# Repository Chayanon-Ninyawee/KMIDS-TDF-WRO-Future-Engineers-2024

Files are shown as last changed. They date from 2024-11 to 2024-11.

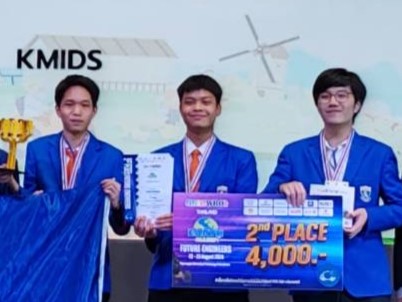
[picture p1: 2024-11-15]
Documentation/Team Picture/Team pic specific.jpg

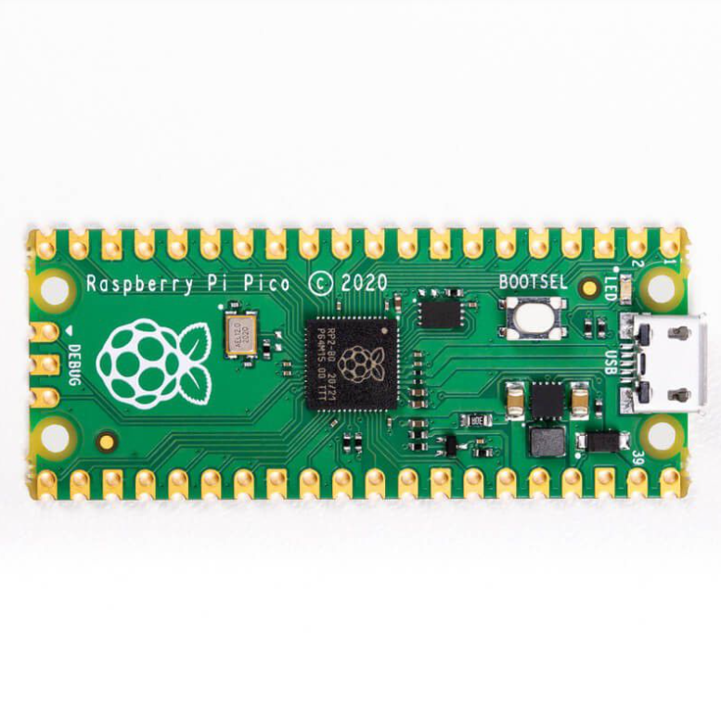
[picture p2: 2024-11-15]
Documentation/Specification/Pi pico.png

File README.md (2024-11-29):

# WRO 2024 Future Engineer
Team: KMIDS Thermodynamically Favorable (KMIDS TDF)

This is a repository for KMIDS Thermodynamically Favorable this project, we aim to design an autonomous robot that can navigate around a field with various rules and restrictions depending on the rounds. In this repository you will find details about our robot: function, design, and reflection from our journey.

New robot
Team member pic

**Member**
- **Left:** Natthapon Itthisathidkulchai (Pao)
- **Middle:** Chayanon Ninyawee (Garfield)
- **Right:** Pannawit Phruithithada (Prame)

## Content
- [RaspberryPi5](https://github.com/Chayanon-Ninyawee/KMIDS-TDF-WRO-Future-Engineers-2024/tree/main/RaspberryPi5) Contains our code for RaspberryPi5 and setup.<!--TODO at link-->
- [RaspberryPiPico](https://github.com/Chayanon-Ninyawee/KMIDS-TDF-WRO-Future-Engineers-2024/tree/main/RaspberryPiPico) Contains our code for RaspberryPiPico and setup.<!--TODO at link-->
- [KMIDS-TDF-WRO2024-FreeCAD](https://github.com/Chayanon-Ninyawee/KMIDS-TDF-WRO-Future-Engineers-2024/tree/main/KMIDS-TDF-WRO2024-FreeCAD) Contains robot's 3D model and electronics.
- [Mobility Management](https://github.com/Chayanon-Ninyawee/KMIDS-TDF-WRO-Future-Engineers-2024/blob/main/Documentation/Mobility_Management/Mobility_Management.md) Contains robot's design and mechanism.
- [Obstacle Management](https://github.com/Chayanon-Ninyawee/KMIDS-TDF-WRO-Future-Engineers-2024/tree/main/Documentation/Obstacle%20Management) Contains how we deal with the obstacle challenges.
- [Power and Senses Management](https://github.com/Chayanon-Ninyawee/KMIDS-TDF-WRO-Future-Engineers-2024/tree/main/Documentation/Power%20and%20Senses%20Management) Contains how we manage our electronics and various sensors.
- [Robot Picture](https://github.com/Chayanon-Ninyawee/KMIDS-TDF-WRO-Future-Engineers-2024/tree/main/Documentation/Robot%20Picture) Contains picture of the robot, both in physical and digital 3D model from FreeCad.
- [Specification](https://github.com/Chayanon-Ninyawee/KMIDS-TDF-WRO-Future-Engineers-2024/tree/main/Documentation/Specification) Contains the specifications of various electronics and parts uses to built this robot.
- [Team Member Picture](https://github.com/Chayanon-Ninyawee/KMIDS-TDF-WRO-Future-Engineers-2024/tree/main/Documentation/Team%20Picture) Contains our team's picture.
- [3D Model](https://github.com/Chayanon-Ninyawee/KMIDS-TDF-WRO-Future-Engineers-2024/tree/fix-readme/Documentation/3D%20model) Contains the process of developing and modeling the chassis.

## Performance video
Our video demonstrating our robot can be found [here](https://youtu.be/9CfIpZZZoUU?si=juIyMaRLtTwPCz_5)
## Design Journey
When designing the robot, our first consideration was its parking strategy. This is a crucial decision, as we had to choose between having the robot reverse into a wall or perform a parallel parking maneuver. Next, we focused on optimizing the robot's turning angle to ensure it could avoid obstacles effectively by maximizing its range of motion. Following that, we moved on to designing the chassis and determining the optimal placement for the various electronic components. A significant challenge during this stage was the limitation of our RPLIDAR C1 sensor, which must be positioned at a precise height to detect the wall properly. Finally, the prototyping phase proved to be the most challenging. We repeatedly faced issues with 3D printing, as the actual printed parts often deviated from the original design, requiring constant adjustments and refinements to achieve the desired results.

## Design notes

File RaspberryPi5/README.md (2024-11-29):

# How to Setup RaspberryPi5
- Insert a microSD card, which should contain 8GB or larger into computer.
- Download, install and run [Raspberry Pi Imager](https://www.raspberrypi.com/software/) that is appropriate for your operating system.
- Click the choose device button and a list of Pi boards appears.
 


- Choose Raspberry Pi 5 in the Pi board. 
  


- Click the Choose OS button and menu will appear. 



- Choose the top choice, Raspberry Pi OS (64-bit), for Pi 5. If there are Raspberry Pi OS on top choice, click that and choose the latest version that works with your board.



- Click Choose Storage and select the card from the menu.



- Click Next 



- Clear and Click Edit Settings 



- Fill in all blank on the General tab: hostname, username / password, wireless LAN (If you plan to use Wi-Fi, and locale settings).



- Go to Serivec Tab, Click Enable SSH button and Select "Use password authentication."  Then click Save.



- Click Yes to apply OS customization settings. !



- Click Yes to confirm that you want to write to your microSD card. !



- It will take a few minutes to download the OS and write it to the card. 



- Once the process is complete, insert the microSD card into your Raspberry Pi, power it on, and give it a few seconds to connect to the network. Then, you can try logging in via SSH, assuming both the Raspberry Pi and your computer are connected to the same Wi-Fi network.

# How to install CMake
``` 
sudo apt install -y cmake
```

# How to Setup OpenCV
## Dependencies
OpenCV needs other software libraries to work, and these must be installed first. Some of them come with the Raspberry Pi 64-bit operating system, and others might already be installed. To be safe, here's the full list. Only the latest packages are installed according to the procedure.
```
# check for updates
sudo apt-get update
sudo apt-get upgrade
# dependencies
sudo apt-get install build-essential cmake git unzip pkg-config
sudo apt-get install libjpeg-dev libpng-dev
sudo apt-get install libavcodec-dev libavformat-dev libswscale-dev
sudo apt-get install libgtk2.0-dev libcanberra-gtk* libgtk-3-dev
sudo apt-get install libgstreamer1.0-dev gstreamer1.0-gtk3
sudo apt-get install libgstreamer-plugins-base1.0-dev gstreamer1.0-gl
sudo apt-get install libxvidcore-dev libx264-dev
sudo apt-get install python3-dev python3-numpy python3-pip
sudo apt-get install libtbb2 libtbb-dev libdc1394-22-dev
sudo apt-get install libv4l-dev v4l-utils
sudo apt-get install libopenblas-dev libatlas-base-dev libblas-dev
sudo apt-get install liblapack-dev gfortran libhdf5-dev
sudo apt-get install libprotobuf-dev libgoogle-glog-dev libgflags-dev
sudo apt-get install protobuf-compiler
```
## Download OpenCV
Once all the third-party software is installed, you can download OpenCV itself. You'll need two packages: the basic version and the additional contributions. After downloading, simply unzip the files. Be careful with line wrapping in the command boxes. The two commands begin with ```wget``` and end with .```zip.```
```
# check your memory first
free -m
# you need at least a total of 5.8 GB!
# if not, enlarge your swap space as explained earlier
# download the latest version
cd ~
git clone --depth=1 https://github.com/opencv/opencv.git
git clone --depth=1 https://github.com/opencv/opencv_contrib.git
```
## Build Make
Before begin with the actual build of the library. You have to make a directory where all the build files can be located.
```
cd ~/opencv
mkdir build
cd build
```
In this step, you instruct CMake on what , where , and how to make OpenCV on your Raspberry Pi. There are several flags to consider, most of which will be familiar to you. One important line you’ll notice is -D WITH_QT=OFF, which disables Qt5 support. If you want to use Qt5 for the GUI, change this to -D WITH_QT=ON. We also save space by excluding any (Python) examples or tests.

Note that there should be spaces before the -D flags, not tabs. Also, the two dots at the end are no typo. It tells CMake where to find its CMakeLists.txt file (the main configuration file); one directory up.
```
cmake -D CMAKE_BUILD_TYPE=RELEASE \
-D CMAKE_INSTALL_PREFIX=/usr/local \
-D OPENCV_EXTRA_MODULES_PATH=~/opencv_contrib/modules \
-D ENABLE_NEON=ON \
-D WITH_OPENMP=ON \
-D WITH_OPENCL=OFF \
-D BUILD_TIFF=ON \
-D WITH_FFMPEG=ON \
-D WITH_TBB=ON \
-D BUILD_TBB=ON \
-D WITH_GSTREAMER=ON \
-D BUILD_TESTS=OFF \
-D WITH_EIGEN=OFF \
-D WITH_V4L=ON \
-D WITH_LIBV4L=ON \
-D WITH_VTK=OFF \
-D WITH_QT=OFF \
-D WITH_PROTOBUF=ON \
-D OPENCV_ENABLE_NONFREE=ON \
-D INSTALL_C_EXAMPLES=OFF \
-D INSTALL_PYTHON_EXAMPLES=OFF \
-D OPENCV_FORCE_LIBATOMIC_COMPILER_CHECK=1 \
-D PYTHON3_PACKAGES_PATH=/usr/lib/python3/dist-packages \
-D OPENCV_GENERATE_PKGCONFIG=ON \
-D BUILD_EXAMPLES=OFF ..
```
CMake comes with a report, showing image below. CMake
## Make
With all compilation directives in place, you can start the build with the following command. This will take about minutes.
```
make -j4
```
Hope that it will show the piture below: 
Install all the generated packages to the database of your system with the next commands.
```
sudo make install
sudo ldconfig
# cleaning (frees 300 KB)
 make clean
sudo apt-get update
```
## Check
Use the following C++ code to check the OpenCV
```
#include <opencv2/opencv.hpp>

int main(void)
{
    std::cout << "OpenCV version : " << cv::CV_VERSION << endl;
    std::cout << "Major version : " << cv::CV_MAJOR_VERSION << endl;
    std::cout << "Minor version : " << cv::CV_MINOR_VERSION << endl;
    std::cout << "Subminor version : " << cv::CV_SUBMINOR_VERSION << endl;
    std::cout << cv::getBuildInformation() << std::endl;
}
```

# How to connect to Raspberry pi 5 via ethernet cable (Open DHCP Server on the Ethernet port in Linux)
- ### Select interface with:
  ```
  sudo nano /etc/default/isc-dhcp-server
  ---
  INTERFACESv4="eno1"
  INTERFACESv6=""

  sudo nano /etc/dhcp/dhcpd.conf
  ---
  subnet 192.168.39.0 netmask 255.255.255.0 {
  range 192.168.39.10 192.168.39.50;
  option subnet-mask 255.255.255.0;
  option routers 192.168.39.1;
  }
  ```

- ### Add new Ethernet Connection
  make the ipv4 address the same as above (192.168.39.1)
- ### How to run:
  ```
  sudo systemctl start isc-dhcp-server.service
  ```
- ### How to check:
  ```
  sudo systemctl status isc-dhcp-server.service
  ```
- ### If error:
  ```
  journalctl _PID=<PID Here>
  ```
- ### Don't forget to make sure the interface is up:
  ```
  ip addr show eno1
  ```
- ### How to autostart:
  ```
  sudo systemctl enable isc-dhcp-server.service
  ```
- ### How to stop autostart:
  ```
  sudo systemctl disable isc-dhcp-server.service
  ```

# ObstacleChallenge Documentation

## Overview

The `ObstacleChallenge` class provides functionality to navigate through obstacle courses using LIDAR and camera data. It incorporates PID controllers for precise control of steering and wall-following distances, state machines for navigation logic, and traffic light detection for enhanced decision-making.

---

## Enums

### `State`
Defines the various states the robot can be in during the obstacle challenge.

- **Values**:
  - `STOP`
  - `NORMAL`
  - `SLOW_BEFORE_TURN`
  - `WAITING_FOR_TURN`
  - `TURNING`
  - `UTURNING_1`
  - `UTURNING_2`
  - `FIND_PARKING_ZONE`
  - `PARKING_1`
  - `PARKING_2`

---

### `TrafficLightRingPosition`
Specifies the ring position of detected traffic lights.

- **Values**:
  - `OUTER`
  - `INNER`

---

### `TrafficLightPosition`
Defines the relative positions of traffic lights.

- **Values**:
  - `BLUE`
  - `MID`
  - `ORANGE`
  - `NO_POSITION`

---

## Structures

### `TrafficLightSearchKey`
Defines a search key for identifying traffic lights.

- **Fields**:
  - `lightPosition`: A `TrafficLightPosition` specifying the traffic light's position.
  - `direction`: A `Direction` enum representing the direction.

#### Operators
- `operator<`: Compares two `TrafficLightSearchKey` objects for ordering.
- `operator==`: Checks equality of two `TrafficLightSearchKey` objects.

#### Hash Function
A custom hash function is defined for use with `std::unordered_set`:
```cpp
namespace std {
    template <>
    struct hash<TrafficLightSearchKey> {
        size_t operator()(const TrafficLightSearchKey& key) const {
            size_t h1 = std::hash<int>{}(static_cast<int>(key.lightPosition));
            size_t h2 = std::hash<int>{}(static_cast<int>(key.direction));
            return h1 ^ (h2 << 1);
        }
    };
}
```

---

## Class: `ObstacleChallenge`

### Constructor
```cpp
ObstacleChallenge(int lidarScale, cv::Point lidarCenter);
```
Initializes an `ObstacleChallenge` object.

- **Parameters**:
  - `lidarScale`: Scale factor for LIDAR data.
  - `lidarCenter`: Center point of the LIDAR map.

---

### Public Methods

#### **`void update`**
```cpp
void update(const cv::Mat& lidarBinaryImage, const cv::Mat& cameraImage, float gyroYaw, float& motorPercent, float& steeringPercent);
```
Updates the robot's state and controls motor and steering based on sensor inputs.

- **Parameters**:
  - `lidarBinaryImage`: Binary image from the LIDAR data.
  - `cameraImage`: Image captured from the camera.
  - `gyroYaw`: Current yaw angle from the gyroscope.
  - `motorPercent`: Motor speed percentage (output parameter).
  - `steeringPercent`: Steering angle percentage (output parameter).

---

### Private Members

#### **PID Controllers**
- `steeringPID`: Controls steering with parameters `Kp = 0.026f`, `Ki = 0.0f`, `Kd = 0.0008f`.
- `wallDistancePID`: Controls wall-following distance with parameters `Kp = 200.0f`, `Ki = 0.0010f`, `Kd = 0.0f`.

#### **Thresholds and Biases**
- `MAX_HEADING_ERROR`: Maximum allowable heading error (`40.0` degrees).
- `MIN_HEADING_ERROR`: Minimum allowable heading error (`-40.0` degrees).
- `FRONT_WALL_DISTANCE_*`: Various thresholds for wall distances, used to make decisions during navigation.
- `wallDistanceBias`: Bias for wall distance control (`0.0f` by default).

#### **State and Cooldown Timers**
- `state`: Current state of the robot (`State::NORMAL` by default).
- `TURN_COOLDOWN`: Cooldown time between turns (`1.1f` seconds).
- `FIND_PARKING_COOLDOWN`: Cooldown time for parking detection (`1.1f` seconds).
- `TRAFFIC_COOLDOWN`: Cooldown time for traffic light processing (`0.8f` seconds).

#### **Traffic Light Handling**
- `trafficLightMap`: Maps `TrafficLightSearchKey` to ring position and color.
- `trafficLightOrderQueue`: Maintains the insertion order of traffic light keys.
- `trafficLightKeySet`: Ensures fast duplicate detection of traffic lights.

#### **Miscellaneous**
- `robotDirection`: Current direction of the robot (`NORTH` by default).
- `turnDirection`: Current turn direction (`UNKNOWN` by default).
- `numberofTurn`: Number of turns completed.

---

## Example Usage
```cpp
#include "ObstacleChallenge.h"
#include <opencv2/opencv.hpp>

int main() {
    cv::Point lidarCenter(100, 100);
    int lidarScale = 10;

    ObstacleChallenge obstacleChallenge(lidarScale, lidarCenter);

    cv::Mat lidarBinaryImage; // Load or initialize LIDAR image
    cv::Mat cameraImage;      // Load or initialize camera image
    float gyroYaw = 0.0f;
    float motorPercent = 0.0f;
    float steeringPercent = 0.0f;

    obstacleChallenge.update(lidarBinaryImage, cameraImage, gyroYaw, motorPercent, steeringPercent);

    // Use motorPercent and steeringPercent as needed
    return 0;
}
```

---

## Licensing

This header file should be used in compliance with the licensing terms of its respective project and dependencies, including OpenCV and any LIDAR processing libraries.

# OpenChallenge Documentation

## Overview

The `OpenChallenge` class provides the logic for navigating an open space using LIDAR data. It employs PID controllers to manage steering and wall distance, and a state machine to handle transitions between different navigation states.

---

## Enums

### `State`
Defines the possible states of the robot during the open challenge.

- **Values**:
  - `STOP`: The robot is stopped.
  - `NORMAL`: The robot is moving forward under normal conditions.
  - `TURNING`: The robot is in a turning state.

---

## Class: `OpenChallenge`

### Constructor
```cpp
OpenChallenge(int lidarScale, cv::Point lidarCenter);
```
Initializes an `OpenChallenge` object.

- **Parameters**:
  - `lidarScale`: Scale factor for the LIDAR data.
  - `lidarCenter`: The center point of the LIDAR map.

---

### Public Methods

#### **`void update`**
```cpp
void update(const cv::Mat& lidarBinaryImage, float gyroYaw, float& motorPercent, float& steeringPercent);
```
Updates the robot's motor and steering outputs based on the LIDAR image and gyro data.

- **Parameters**:
  - `lidarBinaryImage`: Binary image representing the LIDAR data.
  - `gyroYaw`: Current yaw angle from the gyroscope.
  - `motorPercent`: Output parameter for motor speed as a percentage (-1.0 to 1.0).
  - `steeringPercent`: Output parameter for steering angle as a percentage (-1.0 to 1.0).

---

### Private Members

#### **PID Controllers**
- `steeringPID`: Controls steering with parameters:
  - `Kp = 0.017f`
  - `Ki = 0.0f`
  - `Kd = 0.0019f`
- `wallDistancePID`: Controls wall-following with parameters:
  - `Kp = 50.0f`
  - `Ki = 0.0f`
  - `Kd = 0.0030f`

#### **Thresholds and Biases**
- `MAX_HEADING_ERROR`: Maximum allowable heading error (`25.0` degrees).
- `MIN_HEADING_ERROR`: Minimum allowable heading error (`-25.0` degrees).
- `FRONT_WALL_DISTANCE_STOP_THRESHOLD`: Distance at which the robot stops moving forward (`2.200` meters).
- `FRONT_WALL_DISTANCE_SLOWDOWN_THRESHOLD`: Distance at which the robot slows down (`1.000` meters).
- `FRONT_WALL_DISTANCE_TURN_THRESHOLD`: Distance at which the robot initiates a turn (`0.690` meters).
- `OUTER_WALL_DISTANCE`: Distance to maintain from the outer wall (`0.350` meters).
- `MAX_HEADING_ERROR_BEFORE_EXIT_TURNING`: Maximum heading error allowed before exiting a turning state (`10.0` degrees).
- `wallDistanceBias`: Wall distance bias (`0.000` by default, where negative is left bias and positive is right bias).

#### **State and Cooldown Timers**
- `state`: Current state of the robot (`State::NORMAL` by default).
- `lastTurnTime`: Time of the last turn made (`-1.0` seconds by default).
- `TURN_COOLDOWN`: Cooldown time between consecutive turns (`1.0` seconds).
- `STOP_COOLDOWN`: Cooldown time before stopping after a turn (`0.2` seconds).

#### **Navigation Parameters**
- `lidarScale`: Scale of the LIDAR data.
- `lidarCenter`: Center point of the LIDAR map.
- `robotDirection`: Current direction of the robot (`NORTH` by default).
- `turnDirection`: Current turn direction (`UNKNOWN` by default).
- `numberofTurn`: Number of turns completed.

---

## Example Usage

```cpp
#include "OpenChallenge.h"
#include <opencv2/opencv.hpp>

int main() {
    cv::Point lidarCenter(100, 100);
    int lidarScale = 10;

    OpenChallenge openChallenge(lidarScale, lidarCenter);

    cv::Mat lidarBinaryImage; // Initialize or load LIDAR binary image
    float gyroYaw = 0.0f;
    float motorPercent = 0.0f;
    float steeringPercent = 0.0f;

    openChallenge.update(lidarBinaryImage, gyroYaw, motorPercent, steeringPercent);

    // Use motorPercent and steeringPercent for robot control
    return 0;
}
```

---

## Licensing

This file should be used in compliance with the licensing terms of its respective project and any dependencies such as OpenCV.

# BNO055 Struct Documentation

## Overview

This header file defines structures for handling BNO055 sensor data outputs in precision floating-point format. The structures encapsulate data for accelerometer readings and Euler angles.

---

## Structs

### `bno055_accel_float_t`
A structure representing accelerometer output data in floating-point precision.

#### Fields
- `x`: Accelerometer data along the X-axis.
- `y`: Accelerometer data along the Y-axis.
- `z`: Accelerometer data along the Z-axis.

#### Example
```cpp
bno055_accel_float_t accelData;
accelData.x = 1.23f;
accelData.y = 0.45f;
accelData.z = -0.67f;
```

---

### `bno055_euler_float_t`
A structure representing Euler angle output data in floating-point precision.

#### Fields
- `h`: Heading (yaw) angle in degrees.
- `r`: Roll angle in degrees.
- `p`: Pitch angle in degrees.

#### Example
```cpp
bno055_euler_float_t eulerData;
eulerData.h = 90.0f;
eulerData.r = -45.0f;
eulerData.p = 10.0f;
```

---

## Licensing

This file should be used in compliance with the licensing terms of the project it belongs to. The structures are designed for BNO055 sensor integration and should adhere to the sensor's usage guidelines.

---
**Header Guard**: 
```cpp
#ifndef BNO055_STRUCT_H
#define BNO055_STRUCT_H
```
Ensure this file is included only once during compilation.

# DataSaver Documentation

## Overview

The `DataSaver` namespace provides functionality for saving and loading various types of data, including calibration data, LIDAR scan data, BNO055 sensor data, and images. These utilities are designed to simplify data logging and retrieval for robotics applications.

---

## Functions

### `bool saveData`
```cpp
bool saveData(const std::string& filePath, const uint8_t calibData[22], bool append = true);
```
Saves calibration data to a file.

- **Parameters**:
  - `filePath`: Path to the file where the data will be saved.
  - `calibData`: Array containing 22 bytes of calibration data.
  - `append`: If `true`, appends the data to the file (default is `true`).

- **Returns**:
  - `true` if the data was saved successfully, `false` otherwise.

---

### `bool loadData`
```cpp
bool loadData(const std::string& filePath, uint8_t calibData[22]);
```
Loads calibration data from a file.

- **Parameters**:
  - `filePath`: Path to the file from which the data will be loaded.
  - `calibData`: Array to store the 22 bytes of loaded calibration data.

- **Returns**:
  - `true` if the data was loaded successfully, `false` otherwise.

---

### `bool saveLogData`
```cpp
bool saveLogData(const std::string& filePath, 
                 const std::vector<lidarController::NodeData>& scanData, 
                 const bno055_accel_float_t& accel_data, 
                 const bno055_euler_float_t& euler_data, 
                 const cv::Mat& image, 
                 bool append = true);
```
Saves log data including LIDAR scans, accelerometer data, Euler data, and an image.

- **Parameters**:
  - `filePath`: Path to the file where the log data will be saved.
  - `scanData`: Vector of LIDAR scan data.
  - `accel_data`: Accelerometer data (`bno055_accel_float_t`).
  - `euler_data`: Euler angle data (`bno055_euler_float_t`).
  - `image`: Image (`cv::Mat`) to be saved.
  - `append`: If `true`, appends the log data to the file (default is `true`).

- **Returns**:
  - `true` if the log data was saved successfully, `false` otherwise.

---

### `bool loadLogData`
```cpp
bool loadLogData(const std::string& filePath, 
                 std::vector<std::vector<lidarController::NodeData>>& allScanData, 
                 std::vector<bno055_accel_float_t>& allAccelData, 
                 std::vector<bno055_euler_float_t>& allEulerData, 
                 std::vector<cv::Mat>& allImages);
```
Loads log data including LIDAR scans, accelerometer data, Euler data, and images.

- **Parameters**:
  - `filePath`: Path to the file from which the log data will be loaded.
  - `allScanData`: Vector to store multiple sets of LIDAR scan data.
  - `allAccelData`: Vector to store accelerometer data.
  - `allEulerData`: Vector to store Euler angle data.
  - `allImages`: Vector to store images (`cv::Mat`).

- **Returns**:
  - `true` if the log data was loaded successfully, `false` otherwise.

---

## Namespace: `DataSaver`

The functions are encapsulated within the `DataSaver` namespace to avoid name conflicts and improve organization.

---

## Licensing

This file is part of a robotics project and should be used in accordance with its licensing terms.

---
**Header Guard**:
```cpp
#ifndef DATASAVER_H
#define DATASAVER_H
```N    
Ensure this file is included only once during compilation.
# Direction Header Documentation

## Overview

This header file defines enums and functions for managing cardinal and relative directions, including utilities for turning and converting directions to string or heading values.

---

## Enums

### `Direction`
Represents the four cardinal directions.

#### Values:
- `NORTH`
- `EAST`
- `SOUTH`
- `WEST`

---

### `RelativeDirection`
Represents relative movement directions.

#### Values:
- `FRONT`
- `BACK`
- `LEFT`
- `RIGHT`

---

### `TurnDirection`
Represents the possible turn directions.

#### Values:
- `CLOCKWISE`
- `COUNTER_CLOCKWISE`
- `UNKNOWN`

---

## Functions

### `Direction calculateRelativeDirection`
```cpp
Direction calculateRelativeDirection(Direction currentDirection, RelativeDirection relativeMove);
```

Calculates the new direction based on the current direction and a relative move.

#### Parameters:
- `currentDirection`: The current cardinal direction (`Direction`).
- `relativeMove`: The relative move to apply (`RelativeDirection`).

#### Returns:
- A `Direction` representing the new cardinal direction.

#### Example:
```cpp
Direction newDir = calculateRelativeDirection(NORTH, RIGHT);
// newDir will be EAST
```

---

### `std::string directionToString`
```cpp
std::string directionToString(Direction direction);
```

Converts a `Direction` enum value to a human-readable string.

#### Parameters:
- `direction`: A `Direction` enum value.

#### Returns:
- A string representation of the direction (e.g., "NORTH", "EAST").

#### Example:
```cpp
std::string dirStr = directionToString(WEST);
// dirStr will be "WEST"
```

---

### `float directionToHeading`
```cpp
float directionToHeading(Direction direction);
```

Converts a `Direction` enum value to a heading angle in degrees.

#### Parameters:
- `direction`: A `Direction` enum value.

#### Returns:
- A float representing the heading in degrees:
  - `NORTH` → 0°
  - `EAST` → 90°
  - `SOUTH` → 180°
  - `WEST` → 270°

#### Example:
```cpp
float heading = directionToHeading(SOUTH);
// heading will be 180.0f
```

---

## Licensing

This file is part of a robotics or navigation project. Use in compliance with the project's licensing terms.

---

**Header Guard**:
```cpp
#ifndef DIRECTION_H
#define DIRECTION_H
```

Prevents multiple inclusions during compilation.

# I2C Master Library Documentation

This documentation provides an overview of the `i2c_master` library, designed to manage I2C communication between a master device and a slave device. The library includes memory mapping, command structures, and utility functions for sending and receiving data.

## Namespace: `i2c_slave_mem_addr`
Defines memory layout and sizes for the I2C slave's memory map.

### Constants:
- **`MEM_SIZE`**: Total memory size (256 bytes).
- **`COMMAND_SIZE`**: Command register size (1 byte).
- **`STATUS_SIZE`**: Status register size (1 byte).
- **`GYRO_OFFSET_SIZE`**: Gyroscope offset data size (6 bytes).
- **`ACCEL_OFFSET_SIZE`**: Accelerometer offset data size (8 bytes).
- **`MAG_OFFSET_SIZE`**: Magnetometer offset data size (8 bytes).
- **`BNO055_CALIB_SIZE`**: Total calibration data size (22 bytes).
- **`ACCEL_DATA_SIZE`**: Accelerometer data size (12 bytes).
- **`EULER_ANGLE_SIZE`**: Euler angle data size (12 bytes).
- **`BNO055_INFO_SIZE`**: Total sensor info size (24 bytes).
- **`MOTOR_PERCENT_SIZE`**: Motor speed as float (4 bytes).
- **`STEERING_PERCENT_SIZE`**: Steering angle as float (4 bytes).
- **`MOVEMENT_INFO_SIZE`**: Combined movement info size (8 bytes).
- **`LOG_SIZE`**: Size of each log entry (1 byte).
- **`LOGS_BUFFER_SIZE`**: Total logs buffer size (256 bytes).

### Memory Map Addresses:
- **`COMMAND_ADDR`**: Start address of command data.
- **`STATUS_ADDR`**: Start address of status data.
- **`BNO055_CALIB_ADDR`**: Start address of calibration data.
- **`BNO055_INFO_ADDR`**: Start address of sensor info.
- **`MOVEMENT_INFO_ADDR`**: Start address of movement info.
- **`LOG_ADDR`**: Start address of log data.

### Static Assertions:
Ensures memory allocation fits within the defined buffer size.

---

## Enums

### `Command`
Defines available commands for the I2C slave device:
- **`NO_COMMAND (0x00)`**: No operation.
- **`RESTART (0x01)`**: Restart the slave device.
- **`CALIB_NO_OFFSET (0x02)`**: Calibrate without offsets.
- **`CALIB_WITH_OFFSET (0x03)`**: Calibrate with offsets.
- **`SKIP_CALIB (0x04)`**: Skip calibration.

---

## Functions

### Initialization and Setup
#### `int i2c_master_init(uint8_t slave_address)`
Initializes communication with the I2C slave device.
- **Parameters**:
  - `slave_address`: 7-bit address of the I2C slave device.
- **Returns**: File descriptor for the I2C device, or `-1` on failure.

---

### Command and Data Transmission
#### `void i2c_master_send_command(int fd, uint8_t command)`
Sends a command to the I2C slave device.
- **Parameters**:
  - `fd`: File descriptor for the I2C device.
  - `command`: Command byte.

#### `void i2c_master_send_data(int fd, uint8_t reg, uint8_t *data, uint8_t len)`
Sends data to a specific register on the I2C slave device.
- **Parameters**:
  - `fd`: File descriptor for the I2C device.
  - `reg`: Register address to write to.
  - `data`: Pointer to the data buffer.
  - `len`: Length of the data buffer.

#### `void i2c_master_read_data(int fd, uint8_t reg, uint8_t *data, uint8_t len)`
Reads data from a specific register on the I2C slave device.
- **Parameters**:
  - `fd`: File descriptor for the I2C device.
  - `reg`: Register address to read from.
  - `data`: Pointer to the buffer for storing the data.
  - `len`: Number of bytes to read.

---

### Logging Functions
#### `void i2c_master_read_logs(int fd, uint8_t *logs)`
Reads log data from the I2C slave using the default size.
- **Parameters**:
  - `fd`: File descriptor for the I2C device.
  - `logs`: Pointer to the buffer for storing logs.

#### `void i2c_master_read_logs(int fd, uint8_t *logs, size_t len)`
Reads log data with a specified size.
- **Parameters**:
  - `fd`: File descriptor for the I2C device.
  - `logs`: Pointer to the buffer for storing logs.
  - `len`: Number of bytes to read.

#### `void i2c_master_print_logs(uint8_t *logs, size_t len)`
Prints logs in a human-readable format.
- **Parameters**:
  - `logs`: Pointer to the log data buffer.
  - `len`: Length of the log buffer.

---

### Reading Specific Data
#### `void i2c_master_read_command(int fd, uint8_t *command)`
Reads the command byte from the slave.
- **Parameters**:
  - `fd`: File descriptor for the I2C device.
  - `command`: Pointer to the buffer for storing the command byte.

#### `void i2c_master_read_status(int fd, uint8_t *status)`
Reads the status byte from the slave.
- **Parameters**:
  - `fd`: File descriptor for the I2C device.
  - `status`: Pointer to the buffer for storing the status byte.

#### `void i2c_master_read_bno055_calibration(int fd, uint8_t *calibration_data)`
Reads calibration data from the BNO055 sensor.
- **Parameters**:
  - `fd`: File descriptor for the I2C device.
  - `calibration_data`: Pointer to the buffer for storing calibration data.

#### `void i2c_master_read_bno055_info(int fd, uint8_t *info_data)`
Reads sensor data (acceleration and Euler angles).
- **Parameters**:
  - `fd`: File descriptor for the I2C device.
  - `info_data`: Pointer to the buffer for storing sensor data.

#### `void i2c_master_read_movement_info(int fd, uint8_t *movement_info)`
Reads movement information (motor and steering percentages).
- **Parameters**:
  - `fd`: File descriptor for the I2C device.
  - `movement_info`: Pointer to the buffer for storing movement info.

#### `void i2c_master_read_bno055_accel_and_euler(int fd, bno055_accel_float_t *accel_data, bno055_euler_float_t *euler_data)`
Reads both acceleration and Euler angle data from the BNO055.
- **Parameters**:
  - `fd`: File descriptor for the I2C device.
  - `accel_data`: Pointer to the structure for storing acceleration data.
  - `euler_data`: Pointer to the structure for storing Euler angle data.

---

## Conclusion

The `i2c_master` library provides comprehensive support for I2C communication with a focus on sensor data retrieval, logging, and calibration. The modular design ensures easy integration into larger systems.
# Image Processor Library Documentation

This document provides an overview of the `image_processor` library, which uses OpenCV for image processing tasks such as detecting lines, identifying blocks, and processing specific color ranges.

---

## Constants

### General
- **`CROP_PERCENT`**: Ratio to crop the image for processing (50%).

### Color Ranges
Defined as `cv::Scalar` values for lower and upper HSV bounds to detect specific colors:
- **Blue Line**: 
  - `lowerBlueLine = (100, 100, 150)`
  - `upperBlueLine = (140, 220, 220)`
- **Orange Line**: 
  - `lowerOrangeLine = (6, 120, 180)`
  - `upperOrangeLine = (16, 230, 255)`
- **Red Line**: 
  - `lowerRed1Light = (0, 135, 160)`
  - `upperRed1Light = (2, 205, 255)`
  - `lowerRed2Light = (175, 135, 160)`
  - `upperRed2Light = (180, 205, 255)`
- **Green Line**: 
  - `lowerGreen1Light = (55, 70, 120)`
  - `upperGreen1Light = (84, 175, 195)`
  - `lowerGreen2Light = (84, 175, 195)`
  - `upperGreen2Light = (84, 175, 195)`
- **Pink**: 
  - `lowerPinkLight = (165, 244, 200)`
  - `upperPinkLight = (171, 255, 255)`

### Minimum Contour Areas
- **`minBlueLineArea = 37`**
- **`minOrangeLineArea = 37`**
- **`minRedLineArea = 300`**
- **`minGreenLineArea = 300`**

---

## Enums

### `enum class Color`
Defines the color categories used for block detection:
- **`BLUE`**
- **`ORANGE`**
- **`RED`**
- **`GREEN`**
- **`PINK`**

---

## Structs

### `struct Block`
Represents a detected block in the image.
- **`int x`**: X-coordinate of the block.
- **`int y`**: Y-coordinate of the block.
- **`int lowestY`**: Lowest Y-coordinate (for vertical alignment).
- **`int size`**: Size of the block.
- **`Color color`**: Detected color of the block.

### `struct ImageProcessingResult`
Stores the results of the image processing operations.
- **`int blueLineY`**: Y-coordinate of the blue line.
- **`int blueLineSize`**: Size of the blue line.
- **`int orangeLineY`**: Y-coordinate of the orange line.
- **`int orangeLineSize`**: Size of the orange line.
- **`std::vector<Block> blocks`**: Detected blocks.
- **`int pinkX`**: X-coordinate of the pink region.
- **`int pinkY`**: Y-coordinate of the pink region.
- **`int pinkSize`**: Size of the pink region.

---

## Functions

### Utility Functions
#### `std::vector<cv::Point> getCoordinates(const cv::Mat &mask)`
Extracts the coordinates of non-zero pixels in a mask.
- **Parameters**:
  - `mask`: Binary image mask.
- **Returns**: Vector of points with non-zero values.

#### `int getAverageX(const std::vector<cv::Point> &coordinates)`
Calculates the average X-coordinate.
- **Parameters**:
  - `coordinates`: Vector of points.
- **Returns**: Average X-coordinate.

#### `int getAverageY(const std::vector<cv::Point> &coordinates)`
Calculates the average Y-coordinate.
- **Parameters**:
  - `coordinates`: Vector of points.
- **Returns**: Average Y-coordinate.

#### `std::tuple<cv::Point, double, cv::Point> getCentroidAndArea(const std::vector<cv::Point> &contour)`
Calculates the centroid and area of a given contour.
- **Parameters**:
  - `contour`: Vector of points representing a contour.
- **Returns**: Tuple containing:
  - Centroid point.
  - Area of the contour.
  - Additional point for extended centroid information.

---

### Image Processing
#### `ImageProcessingResult processImage(const cv::Mat &image)`
Processes the input image to detect lines, blocks, and colored regions.
- **Parameters**:
  - `image`: Input image.
- **Returns**: Processed results in an `ImageProcessingResult` structure.

#### `cv::Mat filterAllColors(const cv::Mat &image)`
Applies color filtering to detect and highlight all defined color ranges.
- **Parameters**:
  - `image`: Input image.
- **Returns**: Processed image with color filters applied.

---

### Visualization
#### `cv::Mat drawImageProcessingResult(const ImageProcessingResult &result, cv::Mat &image)`
Draws the processing results (lines, blocks, and pink regions) on the input image.
- **Parameters**:
  - `result`: Processing results to visualize.
  - `image`: Input image to draw on.
- **Returns**: Image with visualizations.

---

### Conversion
#### `float pixelToAngle(int pixelX, int imageWidth, int centerOffset, float fov)`
Converts a pixel position to an angle relative to the image's field of view (FoV).
- **Parameters**:
  - `pixelX`: X-coordinate of the pixel.
  - `imageWidth`: Width of the image.
  - `centerOffset`: Offset for the center point.
  - `fov`: Field of view of the camera.
- **Returns**: Angle in degrees.

---

## Conclusion
The `image_processor` library provides comprehensive tools for color-based image analysis and line/block detection. Its modular structure supports real-time processing and visualization for robotics and computer vision applications.
# LibCamera Library Documentation

This documentation details the functionality of the `LibCamera` class, which provides a C++ interface to manage and interact with cameras using the `libcamera` library.

---

## Includes and Dependencies
The library depends on the following headers and libraries:
- **Standard Libraries**:
  - `<atomic>`: For atomic operations.
  - `<iomanip>`: For formatted output.
  - `<iostream>`: For input/output operations.
  - `<limits.h>`: For defining data type limits.
  - `<memory>`: For smart pointers.
  - `<stdint.h>`: For fixed-width integer types.
  - `<string>`: For string manipulation.
  - `<vector>`: For dynamic arrays.
  - `<unordered_map>`: For hash tables.
  - `<queue>`: For FIFO data structure.
  - `<sstream>`: For string streams.
  - `<sys/mman.h>`: For memory management.
  - `<unistd.h>`: For POSIX APIs.
  - `<time.h>`: For time operations.
  - `<mutex>`: For thread synchronization.

- **Libcamera Libraries**:
  - `<libcamera/controls.h>`: For camera control operations.
  - `<libcamera/control_ids.h>`: For control ID management.
  - `<libcamera/property_ids.h>`: For accessing camera properties.
  - `<libcamera/libcamera.h>`: Core libcamera library.
  - `<libcamera/camera.h>`: For camera management.
  - `<libcamera/camera_manager.h>`: For managing camera instances.
  - `<libcamera/framebuffer_allocator.h>`: For allocating frame buffers.
  - `<libcamera/request.h>`: For request handling.
  - `<libcamera/stream.h>`: For stream management.
  - `<libcamera/formats.h>`: For handling data formats.
  - `<libcamera/transform.h>`: For image transformations.

---

## Structs

### `LibcameraOutData`
Represents output data from the camera.
- **`uint8_t *imageData`**: Pointer to the image data.
- **`uint32_t size`**: Size of the image data in bytes.
- **`uint64_t request`**: Identifier for the request.

---

## Class: `LibCamera`

### Overview
The `LibCamera` class is responsible for initializing, configuring, and interacting with a camera device. It supports operations such as capturing frames, setting controls, and managing camera streams.

---

### Public Methods

#### Constructor and Destructor
- **`LibCamera()`**: Default constructor.
- **`~LibCamera()`**: Destructor to clean up resources.

#### Camera Initialization and Configuration
- **`int initCamera()`**: Initializes the camera.
- **`void configureStill(int width, int height, PixelFormat format, int buffercount, Orientation orientation)`**:
  Configures the camera for still image capture.
  - **Parameters**:
    - `width`: Desired image width.
    - `height`: Desired image height.
    - `format`: Pixel format for the images.
    - `buffercount`: Number of frame buffers.
    - `orientation`: Camera orientation.

#### Camera Control and State
- **`int startCamera()`**: Starts the camera capture session.
- **`int resetCamera(int width, int height, PixelFormat format, int buffercount, Orientation orientation)`**:
  Resets the camera with new configuration parameters.
- **`void stopCamera()`**: Stops the camera capture session.
- **`void closeCamera()`**: Closes and releases the camera.

#### Frame Handling
- **`bool readFrame(LibcameraOutData *frameData)`**:
  Reads a frame from the camera.
  - **Parameters**:
    - `frameData`: Pointer to the output frame data structure.
  - **Returns**: `true` if successful, `false` otherwise.
- **`void returnFrameBuffer(LibcameraOutData frameData)`**:
  Returns the frame buffer to the camera for reuse.

#### Control Management
- **`void set(ControlList controls)`**: Sets camera controls using a `ControlList`.

#### Stream Management
- **`Stream *VideoStream(uint32_t *w, uint32_t *h, uint32_t *stride) const`**:
  Retrieves the video stream dimensions.
  - **Parameters**:
    - `w`: Pointer to store the width.
    - `h`: Pointer to store the height.
    - `stride`: Pointer to store the stride.
  - **Returns**: Pointer to the video stream.

#### Camera Information
- **`char *getCameraId()`**: Retrieves the unique identifier of the camera.

---

### Private Methods

#### Capture and Request Management
- **`int startCapture()`**: Begins capturing frames.
- **`int queueRequest(Request *request)`**:
  Queues a request for processing.
  - **Parameters**:
    - `request`: Pointer to the request.
- **`void requestComplete(Request *request)`**:
  Handles a completed request.
- **`void processRequest(Request *request)`**:
  Processes the request and extracts data.

#### Stream Utility
- **`void StreamDimensions(Stream const *stream, uint32_t *w, uint32_t *h, uint32_t *stride) const`**:
  Gets the dimensions of a specific stream.
  - **Parameters**:
    - `stream`: Pointer to the stream.
    - `w`: Pointer to store the width.
    - `h`: Pointer to store the height.
    - `stride`: Pointer to store the stride.

---

### Private Members
- **Camera and Manager**:
  - `unsigned int cameraIndex_`: Index of the camera.
  - `uint64_t last_`: Timestamp of the last operation.
  - `std::unique_ptr<CameraManager> cm`: Camera manager instance.
  - `std::shared_ptr<Camera> camera_`: Shared pointer to the camera.
  - `std::unique_ptr<CameraConfiguration> config_`: Configuration for the camera.
  - `std::unique_ptr<FrameBufferAllocator> allocator_`: Allocator for frame buffers.

- **Request Management**:
  - `std::vector<std::unique_ptr<Request>> requests_`: List of requests.
  - `std::queue<Request *> requestQueue`: Queue of requests.

- **Buffer Management**:
  - `std::map<int, std::pair<void *, unsigned int>> mappedBuffers_`: Mapped buffers for frame data.

- **Streams**:
  - `Stream *viewfinder_stream_`: Pointer to the viewfinder stream.

- **Controls and Synchronization**:
  - `ControlList controls_`: Current controls.
  - `std::mutex control_mutex_`: Mutex for control operations.
  - `std::mutex camera_stop_mutex_`: Mutex for stopping the camera.
  - `std::mutex free_requests_mutex_`: Mutex for managing free requests.

- **Camera Metadata**:
  - `std::string cameraId`: Identifier of the camera.

---

## Conclusion
The `LibCamera` class encapsulates the complexities of working with `libcamera`, offering a high-level interface for camera operations. It supports advanced features such as request management, stream handling, and control configuration, making it suitable for applications requiring precise camera control and data capture.

# LidarController.h Documentation

## Overview

The `LidarController` class provides functionality for controlling and acquiring data from a SLAMTEC LIDAR device. It handles initialization, scanning, data retrieval, and shutdown procedures for the LIDAR sensor.

## Class: `LidarController`

### Constructor: `LidarController(const char* serialPort = "/dev/ttyAMA0", int baudRate = 460800)`
- **Description**: Initializes the `LidarController` object with the provided serial port and baud rate.
- **Parameters**:
  - `serialPort` (default `"/dev/ttyAMA0"`) - The serial port path used to communicate with the LIDAR device.
  - `baudRate` (default `460800`) - Baud rate for communication with the LIDAR device.

### Destructor: `~LidarController()`
- **Description**: Cleans up resources and shuts down the LIDAR when the object is destroyed.

### Method: `bool initialize()`
- **Description**: Initializes the LIDAR driver and establishes a connection with the device.
- **Returns**: `true` if the initialization is successful, `false` otherwise.

### Method: `bool startScanning()`
- **Description**: Starts scanning using the LIDAR. This initiates the motor spin and begins data acquisition.
- **Returns**: `true` if the scan starts successfully, `false` otherwise.

### Method: `void stopScanning()`
- **Description**: Stops the LIDAR scanning process and halts the motor.

### Method: `std::vector<NodeData> getScanData()`
- **Description**: Retrieves scan data from the LIDAR, including angles and distances.
- **Returns**: A vector of `NodeData` containing the scan results.

### Method: `void shutdown()`
- **Description**: Shuts down the LIDAR, stops scanning, and cleans up all resources.

### Method: `static void printScanData(const std::vector<NodeData>& nodeDataVector)`
- **Description**: Prints the LIDAR scan data to the console.
- **Parameters**:
  - `nodeDataVector` - A vector of `NodeData` containing the scan results to be printed.

## Private Members

- `sl::ILidarDriver* lidarDriver` - A pointer to the LIDAR driver instance.
- `sl::IChannel* serialChannel` - A pointer to the communication channel.
- `const char* serialPort` - The serial port used for LIDAR connection.
- `int baudRate` - Baud rate for the communication.

## Dependencies

- `sl_lidar.h` and `sl_lidar_driver.h` - Headers for interacting with the SLAMTEC LIDAR.
- `lidar_struct.h` - A header containing the `NodeData` structure and other necessary definitions.

## Notes
- The `LidarController` class requires a valid SLAMTEC LIDAR device and an appropriate serial port for communication.
# LIDAR Data Processor Documentation

## Overview
The `LIDAR Data Processor` is a C++ library that processes LIDAR data for detecting and analyzing traffic lights, parking zones, and walls. It works by converting raw LIDAR data into a 2D image for further processing using OpenCV techniques. The library can also detect lines, calculate angles, and process data to determine directions for navigation.

## Structures

### `BlockInfo`
Contains information about each detected block in the LIDAR scan.

- `float angle`: The angle of the detected block in degrees.
- `int size`: The size of the block.
- `Color color`: The color of the traffic light associated with the block.

### `ProcessedTrafficLight`
Contains information about each detected traffic light.

- `cv::Point point`: The location of the block.
- `int size`: The size of the block.
- `Color color`: The color of the traffic light.

## Functions

### `cv::Mat lidarDataToImage(const std::vector<lidarController::NodeData> &data, int width, int height, float scale)`
Converts raw LIDAR data into a grayscale OpenCV image. The image will be scaled based on the provided scale factor.

- **Parameters**:
  - `data`: A vector containing the LIDAR data points.
  - `width`: The width of the output image.
  - `height`: The height of the output image.
  - `scale`: A scaling factor to adjust the image resolution.
  
- **Returns**: A grayscale OpenCV image.

### `float toMeter(int scale, double lidarDistance)`
Converts a LIDAR distance into meters, based on the scaling factor.

- **Parameters**:
  - `scale`: The scale factor used for the conversion.
  - `lidarDistance`: The raw distance from the LIDAR.
  
- **Returns**: The distance in meters.

### `std::vector<cv::Vec4i> detectLines(const cv::Mat &binaryImage)`
Detects lines in a binary image using the Hough Line Transform.

- **Parameters**:
  - `binaryImage`: The binary image (after thresholding) to detect lines in.

- **Returns**: A vector of lines represented by four values: `(x1, y1, x2, y2)` for each detected line.

### `double lineLength(const cv::Vec4i& line)`
Calculates the length of a line from the vector `(x1, y1, x2, y2)`.

- **Parameters**:
  - `line`: A vector representing the line with its endpoints.

- **Returns**: The length of the line.

### `double calculateAngle(const cv::Vec4i &line)`
Calculates the angle of a line in degrees.

- **Parameters**:
  - `line`: A vector representing the line with its endpoints.

- **Returns**: The angle of the line in degrees.

### `double pointLinePerpendicularDistance(const cv::Point2f& pt, const cv::Vec4i& line)`
Calculates the perpendicular distance from a point to a line.

- **Parameters**:
  - `pt`: A point.
  - `line`: A line represented by a vector of four points.

- **Returns**: The perpendicular distance from the point to the line.

### `double pointLinePerpendicularDirection(const cv::Point2f& pt, const cv::Vec4i& line)`
Calculates the perpendicular direction from a point to a line.

- **Parameters**:
  - `pt`: A point.
  - `line`: A line represented by a vector of four points.

- **Returns**: The perpendicular direction.

### `double pointToLineSegmentDistance(const cv::Point2f& P, const cv::Vec4i& lineSegment)`
Calculates the perpendicular distance from a point to a line segment.

- **Parameters**:
  - `P`: The point.
  - `lineSegment`: A line segment represented by four points.

- **Returns**: The perpendicular distance from the point to the line segment.

### `cv::Vec4i extendLine(const cv::Vec4i& line, double factor)`
Extends a line by a given factor.

- **Parameters**:
  - `line`: A vector representing the line.
  - `factor`: The factor by which to extend the line.

- **Returns**: The extended line.

### `bool areLinesAligned(const cv::Vec4i& line1, const cv::Vec4i& line2, double angleThreshold, double collinearThreshold)`
Checks if two lines are aligned and collinear within specified thresholds.

- **Parameters**:
  - `line1`: The first line.
  - `line2`: The second line.
  - `angleThreshold`: The angle threshold for alignment.
  - `collinearThreshold`: The threshold for collinearity.

- **Returns**: `true` if the lines are aligned and collinear, otherwise `false`.

### `std::vector<cv::Vec4i> combineAlignedLines(std::vector<cv::Vec4i> lines, double angleThreshold = 12.0, double collinearThreshold = 10.0)`
Combines aligned and collinear lines into a single line.

- **Parameters**:
  - `lines`: A vector of lines.
  - `angleThreshold`: The threshold for angle alignment (default 12.0 degrees).
  - `collinearThreshold`: The threshold for collinearity (default 10.0).

- **Returns**: A vector of combined lines.

### `std::vector<Direction> analyzeWallDirection(const std::vector<cv::Vec4i>& combinedLines, float gyroYaw, const cv::Point& center)`
Analyzes the directions of walls based on the combined lines and gyro data.

- **Parameters**:
  - `combinedLines`: A vector of combined lines.
  - `gyroYaw`: The yaw value from the gyro sensor.
  - `center`: The center point of the analysis.

- **Returns**: A vector of directions (NORTH, EAST, SOUTH, WEST).

### `std::vector<cv::Point> detectTrafficLight(const cv::Mat& binaryImage, const std::vector<cv::Vec4i>& combinedLines, const std::vector<Direction>& wallDirections, TurnDirection turnDirection, Direction direction)`
Detects traffic light positions in the binary image based on the lines and directions.

- **Parameters**:
  - `binaryImage`: The binary image.
  - `combinedLines`: A vector of combined lines.
  - `wallDirections`: A vector of wall directions.
  - `turnDirection`: The turn direction (LEFT, RIGHT, etc.).
  - `direction`: The current direction.

- **Returns**: A vector of points representing the traffic light locations.

### `std::vector<cv::Vec4i> detectParkingZone(const cv::Mat& binaryImage, const std::vector<cv::Vec4i>& combinedLines, const std::vector<Direction>& wallDirections, TurnDirection turnDirection, Direction direction)`
Detects parking zones in the binary image based on the lines and directions.

- **Parameters**:
  - `binaryImage`: The binary image.
  - `combinedLines`: A vector of combined lines.
  - `wallDirections`: A vector of wall directions.
  - `turnDirection`: The turn direction.
  - `direction`: The current direction.

- **Returns**: A vector of parking zone lines.

### `std::vector<ProcessedTrafficLight> processTrafficLight(const std::vector<cv::Point>& trafficLightPoints, const std::vector<BlockInfo>& blockAngles, const cv::Point& center)`
Processes the detected traffic lights and classifies them.

- **Parameters**:
  - `trafficLightPoints`: A vector of points where traffic lights are located.
  - `blockAngles`: A vector of `BlockInfo` containing block angle data.
  - `center`: The center point of the analysis.

- **Returns**: A vector of `ProcessedTrafficLight` containing processed traffic lights.

### `TurnDirection lidarDetectTurnDirection(const std::vector<cv::Vec4i>& combinedLines, const std::vector<Direction>& wallDirections, Direction direction)`
Detects the turn direction based on the combined lines and wall directions.

- **Parameters**:
  - `combinedLines`: A vector of combined lines.
  - `wallDirections`: A vector of wall directions.
  - `direction`: The current direction.

- **Returns**: The detected turn direction.

### `void drawAllLines(cv::Mat &outputImage, const std::vector<cv::Vec4i> &lines, const std::vector<Direction> &wallDirections)`
Draws all the lines on the output image.

- **Parameters**:
  - `outputImage`: The output image to draw on.
  - `lines`: A vector of lines.
  - `wallDirections`: A vector of wall directions.

### `void drawTrafficLights(cv::Mat& outputImage, const std::vector<ProcessedTrafficLight>& processedBlocks)`
Draws the processed traffic lights on the output image.

- **Parameters**:
  - `outputImage`: The output image to draw on.
  - `processedBlocks`: A vector of processed traffic lights.
# LIDAR Struct Documentation

## Overview
The `LIDAR Struct` is a simple C++ structure that holds data for each LIDAR scan node. It stores information about the angle and distance of a detected point in the LIDAR scan.

## Structures

### `NodeData`
This structure represents a single LIDAR scan node.

- `float angle`: The angle of the detected point in the scan, typically in degrees. This indicates the orientation of the point relative to the LIDAR's current position.
- `float distance`: The distance of the detected point from the LIDAR, typically in meters. This represents how far away the point is from the LIDAR sensor.

## Usage
The `NodeData` structure is commonly used to store and process individual points from LIDAR scans, which can then be used for visualization, navigation, or other analysis tasks.

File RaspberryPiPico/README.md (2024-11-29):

# How To Install CMake for Window 10/11
- Go to the [website](https://cmake.org/download/) and download the latest version.
  
- Double click to run the installer.

- When asked for selecting option, select “Add CMake to the system PATH for all users”. Then click install and finish button. 

Option

- Add the path to the environment variables. You have to open “Edit the system environment variables”. Environment Variable

- Click “Environment Variables”.

Button

- Go to “System Variables” and click on “path”. 

Path

- Add the path of the CMake folder along with its bin file. 

- To check installation, open the command prompt and type "cmake"

# How To Install GCC Compiler for Windows 10/11
- Open the [link](https://sourceforge.net/projects/mingw-w64/) and click the “Download” button to download the MinGW-w64 - for 32 and 64 bit Windows. download

- After downloading, you must extract the zip file by right click and choose extract all option and install the folder and “mingw-get-setup” application. 

zip folder

- Click Install Button. 

Install button

- It will appear Installation preferences. Keep this as default and don’t change anything. Click on the “Continue” button and it will move to the next page.

Installation preferences

- Wait downloading the “MinGW Installation Manager” as shown in the image below. downloading manager

- It is mandatory to mark “mingw-developer-tool” (provide some necessary developer tools) and “mingw32-base” (basic MinGW installation). As the image below, there are multiple versions of GNU Compilers. It depends on your needs, and which compiler you want to install. 

Compilers

- Click on the “Apply Changes” to install all the libraries, header-files and modules of the GNU Compiler that selected. Apply Change

- Add the path to the environment variables. You have to open “Edit the system environment variables”. Environment Variable

- Click “Environment Variables”. 

Button

- Go to “System Variables” and click on “path”. 

Path

- Add the path of the MinGW folder along with its bin file. 

Add path

- It is good to go now. Open commander prompt and the image below should show the g++ version installed. 

finish installation 

# Raspberry Pi Pico SDK
## Get SDK code
The [master](https://github.com/raspberrypi/pico-sdk/tree/master/) branch of ```pico-sdk``` on GitHub contains the latest stable release of the SDK. If you need or want to test upcoming features, you can try the [develop](https://github.com/raspberrypi/pico-sdk/tree/develop/) branch instead.
## Visual (VS) code
- Install [the Raspberry Pi Pico Visual Studio Code extension](https://marketplace.visualstudio.com/items?itemName=raspberry-pi.raspberry-pi-pico) in VS Code.
## Installing and Setup
These instructions and steps are Linux-based only. For other platforms and detailed steps, we suggest you look at [Raspberry Pi Pico-Series C/C++ SDK](https://datasheets.raspberrypi.com/pico/raspberry-pi-pico-c-sdk.pdf)
- Install CMake and GCC Complier for Linux
```
sudo apt install cmake gcc-arm-none-eabi libnewlib-arm-none-eabi libstdc++-arm-none-eabi-newlib
```
- There are multiple ways to set up project to point to use the Raspberry Pi Pico SDK:
### - Cloning the SDK locally
1. ```git clone``` Raspberry Pi Pico SDK from this [repository](https://github.com/raspberrypi/pico-sdk/tree/develop/?tab=readme-ov-file)
2. Copy [pico_sdk_import.cmake](https://github.com/raspberrypi/pico-sdk/blob/master/external/pico_sdk_import.cmake) from the SDK into project directory.
3. Set ```PICO_SDK_PATH``` to the SDK location in environment, or pass it (```-DPICO_SDK_PATH=```) to cmake later.
4. Setup a CMakeLists.txt like:
```
cmake_minimum_required(VERSION 3.13...3.27)

# initialize the SDK based on PICO_SDK_PATH
# note: this must happen before project()
include(pico_sdk_import.cmake)

project(my_project)

# initialize the Raspberry Pi Pico SDK
pico_sdk_init()

# rest of project

```      
### - Setup with the Raspberry Pi Pico SDK as a submodule
1. Clone the SDK as a submodule ```called pico-sdk```
2. Setup a ```CMakeLists.txt``` like:
```
cmake_minimum_required(VERSION 3.13...3.27)

# initialize pico-sdk from submodule
# note: this must happen before project()
include(pico-sdk/pico_sdk_init.cmake)

project(my_project)

# initialize the Raspberry Pi Pico SDK
pico_sdk_init()

# rest of project

```
### - Set up with automatic download from GitHub
1. Copy [pico_sdk_import.cmake](https://github.com/raspberrypi/pico-sdk/blob/master/external/pico_sdk_import.cmake) from the SDK into project directory
2. Setup a ```CMakeLists.txt``` like:
```
cmake_minimum_required(VERSION 3.13)

# initialize pico-sdk from GIT
# (note this can come from environment, CMake cache etc)
set(PICO_SDK_FETCH_FROM_GIT on)

# pico_sdk_import.cmake is a single file copied from this SDK
# note: this must happen before project()
include(pico_sdk_import.cmake)

project(my_project)

# initialize the Raspberry Pi Pico SDK
pico_sdk_init()

# rest of project
```
### - Cloning the SDK locally, but without copying ```pico_sdk_import.cmake```
1. ```git clone``` from this [Raspberry Pi Pico SDK repository](https://github.com/raspberrypi/pico-sdk/tree/develop/?tab=readme-ov-file)
2. Setup a ```CMakeLists.txt``` like:
```
cmake_minimum_required(VERSION 3.13)

# initialize the SDK directly
include(/path/to/pico-sdk/pico_sdk_init.cmake)

project(my_project)

# initialize the Raspberry Pi Pico SDK
pico_sdk_init()

# rest of project

```
- Write  code using:
```
#include <stdio.h>
#include "pico/stdlib.h"

int main() {
    stdio_init_all();
    printf("Hello, world!\n");
    return 0;
}
```
- Then, add the following to ```CMakeLists.txt```:
```
add_executable(hello_world
    hello_world.c
)

# Add pico_stdlib library which aggregates commonly used features
target_link_libraries(hello_world pico_stdlib)

# create map/bin/hex/uf2 file in addition to ELF.
pico_add_extra_outputs(hello_world)
```
Note that this example uses the default UART for stdout. If you'd like to use the default USB, refer to the [hello-usb](https://github.com/raspberrypi/pico-examples/tree/master/hello_world/usb) example.

- Setup a CMake build directory. For example, if not using an IDE:
```
$ mkdir build
$ cd build
$ cmake ..
```
When building for a board other than the Raspberry Pi Pico, you should include ```-DPICO_BOARD=board_name``` in the cmake command, for example, ```cmake -DPICO_BOARD=pico2 ..``` or ```cmake -DPICO_BOARD=pico_w ..```. This ensures the SDK and build options are correctly configured for the specified board.

By specifying ```PICO_BOARD=<boardname>```, you define various compiler settings (such as default pin numbers for UART and other hardware). In some cases, it also enables the use of additional libraries (like wireless support for ```PICO_BOARD=pico_w```), which require hardware features available only on specific boards.
- Make your target from the build directory you created:
```
$ make hello_world
```
- You now have ```hello_world.elf``` to load via a debugger, or ```hello_world.uf2``` that can be installed and run on your Raspberry Pi Pico-series device via drag and drop.
# BNO055 Utils Documentation

## Overview
This header file contains utility functions and structures for working with the BNO055 sensor, a 9-axis motion tracking device. The file provides functions for initializing the sensor, calibrating it, and loading calibration offsets. It is designed for use with the Raspberry Pi Pico platform using the `pico/stdlib` library and the `bno055` sensor library.

## Constants

- `BNO055_POWER_MODE`: The power mode for the BNO055 sensor. Set to `BNO055_POWER_MODE_NORMAL`, which provides normal operating power consumption.
- `BNO055_OPERATION_MODE`: The operation mode for the BNO055 sensor. Set to `BNO055_OPERATION_MODE_NDOF` (Nine Degrees of Freedom), which enables the sensor to provide a complete set of motion and orientation data.

## Type Definitions

- `bno055_t`: A typedef for the `bno055` structure, which represents the BNO055 sensor instance.
- `bno055_gyro_offset_t`: A typedef for the structure that stores the gyroscope offset data for calibration.
- `bno055_accel_offset_t`: A typedef for the structure that stores the accelerometer offset data for calibration.
- `bno055_mag_offset_t`: A typedef for the structure that stores the magnetometer offset data for calibration.
- `bno055_accel_float_t`: A typedef for the structure that holds accelerometer data in floating-point format.
- `bno055_euler_float_t`: A typedef for the structure that holds Euler angle data (rotation angles) in floating-point format.

## Functions

### `int8_t bno055_initialize(bno055_t *bno, i2c_inst_t *i2c)`
- **Description**: Initializes the BNO055 sensor.
- **Parameters**:
  - `bno`: A pointer to the `bno055_t` structure representing the sensor instance.
  - `i2c`: An instance of the I2C interface to communicate with the sensor.
- **Return Value**: Returns `0` on successful initialization, or a negative value indicating an error.

### `int8_t bno055_calibrate(bno055_gyro_offset_t *gyroOffset, bno055_accel_offset_t *accelOffset, bno055_mag_offset_t *magOffset)`
- **Description**: Calibrates the BNO055 sensor. This function adjusts the sensor offsets for the gyroscope, accelerometer, and magnetometer.
- **Parameters**:
  - `gyroOffset`: A pointer to the `bno055_gyro_offset_t` structure containing the gyroscope offsets.
  - `accelOffset`: A pointer to the `bno055_accel_offset_t` structure containing the accelerometer offsets.
  - `magOffset`: A pointer to the `bno055_mag_offset_t` structure containing the magnetometer offsets.
- **Return Value**: Returns `0` on successful calibration, or a negative value indicating an error.

### `int8_t bno055_load_offset(bno055_gyro_offset_t *gyroOffset, bno055_accel_offset_t *accelOffset, bno055_mag_offset_t *magOffset)`
- **Description**: Loads previously stored calibration offsets into the BNO055 sensor.
- **Parameters**:
  - `gyroOffset`: A pointer to the `bno055_gyro_offset_t` structure containing the gyroscope offsets to be loaded.
  - `accelOffset`: A pointer to the `bno055_accel_offset_t` structure containing the accelerometer offsets to be loaded.
  - `magOffset`: A pointer to the `bno055_mag_offset_t` structure containing the magnetometer offsets to be loaded.
- **Return Value**: Returns `0` on successful offset loading, or a negative value indicating an error.

## Usage

The BNO055 sensor is initialized by calling `bno055_initialize()`, which sets up communication with the sensor over I2C. Calibration can be performed using the `bno055_calibrate()` function, and once the sensor is calibrated, offsets can be loaded with `bno055_load_offset()`.

This header file provides a foundation for working with the BNO055 sensor on platforms such as the Raspberry Pi Pico, and can be extended to provide additional functionality as needed.

# Debug Print Header Documentation

## Overview

This header file provides functionality for conditional debug logging in C programs. It allows for debug messages to be printed to the console and optionally appended to log files. The logging behavior is controlled through the `DEBUG` macro, enabling or disabling the logging based on the build configuration.

## Preprocessor Directives

### `#define DEBUG`

The `DEBUG` macro is used to enable or disable debug logging in the code. If `DEBUG` is defined, debug logging will be enabled. If not, the debug print macros will be excluded from the code to reduce overhead in production environments.

### `#ifndef NO_LOG`

This directive checks if the `NO_LOG` macro is defined. If `NO_LOG` is not defined, debug logs will be both printed to the console and appended to a log file. If `NO_LOG` is defined, debug messages will only be printed to the console and not logged.

## Debug Print Macro

### `#define DEBUG_PRINT(...)`

This macro is used to log debug messages. The behavior of the macro depends on the `DEBUG` and `NO_LOG` macros:

- If `DEBUG` is defined and `NO_LOG` is not defined:
    - The message is printed to the console using `printf`.
    - The message is then formatted into a buffer and appended to a log using the `append_logs` function, which writes the logs to persistent storage.
    
- If `DEBUG` is defined and `NO_LOG` is defined:
    - The message is only printed to the console using `printf`, without appending to logs.

- If `DEBUG` is not defined:
    - The macro does nothing, effectively removing the debug log statements from the code to optimize for production.

### Example Usage

# I2C Slave Utilities Header Documentation

## Overview

This header file defines utilities for managing an I2C slave interface. It includes functionality for managing memory space for various data structures, setting and retrieving commands, storing BNO055 sensor data, and appending logs in a rolling buffer. The memory layout and commands are well defined to interact with the I2C slave system.

## Namespace: `i2c_slave_mem_addr`

This namespace holds constants and macros to define memory sizes, addresses, and layout for the I2C slave memory.

### Constants

- `MEM_SIZE`: Total memory size allocated for the I2C slave. Set to 256 bytes.
- `COMMAND_SIZE`: Size of the command byte (1 byte).
- `STATUS_SIZE`: Size of the status byte (1 byte).
- `GYRO_OFFSET_SIZE`: Size of the gyro offset data structure.
- `ACCEL_OFFSET_SIZE`: Size of the accelerometer offset data structure.
- `MAG_OFFSET_SIZE`: Size of the magnetometer offset data structure.
- `BNO055_CALIB_SIZE`: Total size of BNO055 calibration data (sum of the gyro, accelerometer, and magnetometer offsets).
- `ACCEL_DATA_SIZE`: Size of the accelerometer data structure.
- `EULER_ANGLE_SIZE`: Size of the Euler angles data structure.
- `BNO055_INFO_SIZE`: Total size of BNO055 information (sum of accelerometer data and Euler angles).
- `MOTOR_PERCENT_SIZE`: Size of the motor percentage data (float).
- `STEERING_PERCENT_SIZE`: Size of the steering percentage data (float).
- `MOVEMENT_INFO_SIZE`: Total size of movement information (sum of motor and steering percentages).
- `LOG_SIZE`: Size of a single log entry (1 byte).
- `LOGS_BUFFER_SIZE`: Size of the log buffer (256 bytes).
- `COMMAND_ADDR`: Starting address for the command data.
- `STATUS_ADDR`: Address for status data.
- `BNO055_CALIB_ADDR`: Address for BNO055 calibration data.
- `BNO055_INFO_ADDR`: Address for BNO055 information data.
- `MOVEMENT_INFO_ADDR`: Address for movement information.
- `LOG_ADDR`: Address for log data.

A static assertion ensures that the total memory allocation fits within the defined memory size.

## Enum: `Command`

This enum defines the available commands for the I2C slave

# PWM Utilities Documentation

This header file defines a set of utility functions for controlling PWM (Pulse Width Modulation) on GPIO pins. These functions are used to configure PWM output for general purposes, servo motors, and motor drivers such as the L9110S.

## Header File Overview

```c
#ifndef PWM_UTILS_H
#define PWM_UTILS_H

#include "hardware/clocks.h"
#include "hardware/gpio.h"
#include "hardware/irq.h"
#include "hardware/pwm.h"
```

This section includes the necessary libraries for controlling hardware clocks, GPIO pins, interrupts, and PWM functionality.

## Function Documentation

### `void setup_pwm(uint gpio_pin, float freq);`

**Description:**

Configures a GPIO pin for PWM output with the specified frequency.

**Parameters:**

- `gpio_pin`: GPIO pin number to be configured for PWM.
- `freq`: Desired PWM frequency in Hz.

**Details:**

This function assigns the given GPIO pin to a PWM slice and calculates the necessary clock divider to generate the desired frequency.

---

### `void enable_pwm(uint gpio_pin, float duty_cycle);`

**Description:**

Enables PWM output on a specified GPIO pin with a defined duty cycle.

**Parameters:**

- `gpio_pin`: GPIO pin number for PWM output.
- `duty_cycle`: Duty cycle as a fraction (0.0 - 1.0), where 1.0 represents 100%.

**Details:**

This function sets the PWM duty cycle to the specified value and enables PWM output on the given GPIO pin.

---

### `void disable_pwm(uint gpio_pin);`

**Description:**

Disables PWM output on a specified GPIO pin.

**Parameters:**

- `gpio_pin`: GPIO pin number where PWM is to be disabled.

**Details:**

This function turns off the PWM output by deactivating the PWM slice associated with the given GPIO pin.

---

### `void setup_servo(uint servo_pin, uint start_angle);`

**Description:**

Initializes a GPIO pin for servo control and sets the initial angle.

**Parameters:**

- `servo_pin`: GPIO pin number connected to the servo.
- `start_angle`: Initial angle of the servo in degrees (0 - 180).

**Details:**

This function sets up the PWM signal for a servo motor at a frequency of 50 Hz and positions the servo to the specified starting angle.

---

### `void set_servo_angle(uint servo_pin, uint angle);`

**Description:**

Sets the angle of a servo motor connected to a specified GPIO pin.

**Parameters:**

- `servo_pin`: GPIO pin number connected to the servo.
- `angle`: Desired angle in degrees (0 - 180).

**Details:**

This function adjusts the PWM duty cycle to move the servo to the desired angle. The angle is converted to the corresponding PWM signal.

---

### `void setup_L9110S_motor_driver(uint motorA_pin, uint motorB_pin);`

**Description:**

Configures two GPIO pins for use with an L9110S motor driver.

**Parameters:**

- `motorA_pin`: GPIO pin connected to the motor driver's A input.
- `motorB_pin`: GPIO pin connected to the motor driver's B input.

**Details:**

This function sets up the L9110S motor driver by configuring the GPIO pins for PWM output and initializing the duty cycle to 0.

---

### `void set_L9110S_motor_speed(uint motorA_pin, uint motorB_pin, float speed);`

**Description:**

Controls the speed and direction of a motor connected to an L9110S driver.

**Parameters:**

- `motorA_pin`: GPIO pin connected to the motor driver's A input.
- `motorB_pin`: GPIO pin connected to the motor driver's B input.
- `speed`: Motor speed as a fraction (-1.0 to 1.0), where positive values represent forward rotation and negative values represent reverse rotation.

**Details:**

This function adjusts the PWM duty cycle on the motor driver inputs to control motor speed and direction. A speed value of `0` stops the motor.

---

## End of File

```c
#endif // PWM_UTILS_H
```

This preprocessor directive ensures that the header file is included only once during compilation.

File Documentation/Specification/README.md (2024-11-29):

## Chassis
  - Material: Plastic (pla+ from esun)
  - Description: The chassis for our robot is made with 3D printer to facilitate a chassis that
    is durable and flexible to endure the stress that is put on it in the competition. The 3D
    printer also allowed us to prototype various parts in quick succession, creating an effective
    workflow.

## Specification
  |Section|Component|Description|Image|
  |-------|---------|-----------|-----|
  |Wheels|[69916 TAMIYA Robot Sports Tire](https://shopee.co.th/69916-TAMIYA-Robot-Sports-Tire-Set-(56mm-Dia.-Clear-Wheels)-i.17469725.6833009480) |A small rubber tire that is made to be in a miniature robot. The size of the wheels provides our robot with a more compact design, which helps in parking.|Tamiya Tires|
  |Motor|[3V 1350RPM DC Micro Metal Gearmotor](https://th.cytron.io/p-3v-1350rpm-dc-micro-metal-gearmotor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)|This motor offers a powerful rotation in small sizes that we see as beneficial in our robot as it allows us to make a more compact design for the robot, which makes for narrower turns.|DC gear motor|
  |Servo|[MG90S Metal Gear Micro Servo](https://th.cytron.io/c-dc-motor/p-mg90s-metal-gear-micro-servo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)|This servo possesses a lot of gear, which helps in refining our control and the precision of the robot, which is crucial when making a turn at an extreme angle to avoid obstacles in quick succession.|MG90S|
  |Processing Unit|[Raspberry pi V5](https://th.cytron.io/c-carrier-board-for-rpi-cm/p-raspberry-pi-5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)|Used to process the video from the camera, which calculates where and in what direction the robot should be headed.|Pi v5|
  |Processing Unit|[Raspberry pi pico](https://th.cytron.io/p-raspberry-pi-pico?srsltid=AfmBOop-tQfKoMxJU1gJo2nNFrc_FSLUJof0p1Rg2VGSW7uQmTslqJTn)|This helps in commanding other components that Raspberry Pi v5 does not|Pi pico|
  |Vision system|[Raspberry pi fisheye len camera](https://th.cytron.io/p-fish-eye-lense-raspberry-pi-5mp-ir-camera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)|The Raspberry Pi camera integrates easily with the Raspberry Pi and provides clear images in a wide area. Making the algorithm more effective as it's able to receive a wider view of the field.|Camera|
  |Distance Sensing|[RPLIDAR C1](https://shopee.co.th/Kiki-RPLIDAR-C1-%E0%B9%82%E0%B8%A1%E0%B8%94%E0%B8%B9%E0%B8%A5%E0%B9%80%E0%B8%8B%E0%B8%99%E0%B9%80%E0%B8%8B%E0%B8%AD%E0%B8%A3%E0%B9%8C%E0%B8%95%E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)|Detect objects at a 360-degree angle and within the range of 12 meters. It also takes 5,000 samples per second, providing clear and accurate readings.|lidar|
  |Color Sensing|[Light Sensor TC01](https://shopee.co.th/%E0%B9%80%E0%B8%8B%E0%B9%87%E0%B8%99%E0%B9%80%E0%B8%8B%E0%B8%AD%E0%B8%A3%E0%B9%8C%E0%B8%88%E0%B8%B1%E0%B8%9A%E0%B9%80%E0%B8%AA%E0%B9%89%E0%B8%99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)|Detect objects' color|Light Sensor|
  |Power Supply|Lithium ion batteries|Provides power for the robot|lithium ion batteries|
  |Orientation and motion Sensing|[BNO055](https://shopee.co.th/BNO055-%E0%B9%82%E0%B8%A1%E0%B8%94%E0%B8%B9%E0%B8%A5%E0%B9%80%E0%B8%8B%E0%B9%87%E0%B8%99%E0%B9%80%E0%B8%8B%E0%B8%AD%E0%B8%A3%E0%B9%8C-9-DOF-%E0%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)|Measures acceleration and orientation comes with accelerometer, gyroscope, magnetometer|BNO055|
  |Motor Control|[L9110S H-bridge Stepper Motor Dual DC Driver Controller Board](https://shopee.co.th/product/5401692/1540697025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)|Control and regulate the 3V 1350RPM DC Micro Metal Gearmotor|H-bridge|

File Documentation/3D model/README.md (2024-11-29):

# 3D Model
Our 3D model was created using FreeCAD from the [realthunder](https://github.com/realthunder/FreeCAD/releases) version, an open-source CAD software that provides broad accessibility for developers in the field of 3D modeling. The model can be viewed in the file [KMIDS-TDF-WRO2024-FreeCAD](https://github.com/Chayanon-Ninyawee/KMIDS-TDF-WRO-Future-Engineers-2024/tree/main/KMIDS-TDF-WRO2024-FreeCAD) by opening the [MainAssembly](https://github.com/Chayanon-Ninyawee/KMIDS-TDF-WRO-Future-Engineers-2024/tree/main/KMIDS-TDF-WRO2024-FreeCAD/MainAssembly) and exported into [STL file](https://github.com/Chayanon-Ninyawee/KMIDS-TDF-WRO-Future-Engineers-2024/tree/main/STL-Files). We use Cura for slicing the models and convert them into [Cura file](https://github.com/Chayanon-Ninyawee/KMIDS-TDF-WRO-Future-Engineers-2024/tree/main/Cura-Files) for preparing printing the chassis of our robot by using `Creality Ender-3 V3 printer`, though other 3D printer can work as well. You can look our model [here](https://github.com/Chayanon-Ninyawee/KMIDS-TDF-WRO-Future-Engineers-2024/tree/fix-readme/Documentation/Robot%20Picture/3D%20models).  

# How to Install FreeCad

- Download FreeCAD realthunder branch [here](https://github.com/realthunder/FreeCAD/releases). 
- Choose an asset that is appropriate for you operating system.

## Window 11/10
 - Click and download the asset link that is appropriate with Windows 11. For example, [FreeCAD-Link-Stable-Win-x86_64-py3.11-20241003.7z file](https://github.com/realthunder/FreeCAD/releases/download/20241003stable/FreeCAD-Link-Stable-Win-x86_64-py3.11-20241003.7z-SHA256.txt)
- Extracted all files by clicking right click and choose "Extract all files" option. 
- Double click the RunFreeCad in the asset folder to run FreeCAD.
## Linux
- Click and download the asset link [org.freecadweb.FreeCAD.Link.Stable_20241003.flatpak](https://github.com/realthunder/FreeCAD/releases/download/20241003stable/org.freecadweb.FreeCAD.Link.Stable_20241003.flatpak)
- Then, run Freecad when download is done.
# FreeCad
- It is opne-source 3D modeler software which is free to use. It supports a wide range of plugins and add-ons, and we can create their own modules to extend its functionality. Whether we're designing simple or complex parts, FreeCAD can be adapted to our needs. It is also cross-platform that allow us to run in any operating system suhc as, Windoe, MacOS, an Linux easily. Moreover, FreeCAD is a great choice for 3D printing, allowing us to create models and export them in formats like [STL file](https://github.com/Chayanon-Ninyawee/KMIDS-TDF-WRO-Future-Engineers-2024/tree/main/STL-Files) and offers tools for checking models to make sure that they can be printed successfully. 
# Cura
- Like FreeCad, Cura is open-source software. It has an interface that allows us to use it easily. Its simple setup process allows us to quickly prepare printing 3D models without extensive learning. It also offers advanced slicing options for experienced users. Here is the [Cura file](https://github.com/Chayanon-Ninyawee/KMIDS-TDF-WRO-Future-Engineers-2024/tree/main/Cura-Files) that we use to print.
# Creality Ender 3D V3
- We decide to use the Creality Ender 3 V3 for 3D printing. It appeals to beginner and expert users. Not only is its price affordable, but it also does not take too long to produce high-quality prints with good detail and precision. It also supports various filament types (PLA, ABS, PETG, TPU, and others). In our case, we use PLA plastic due to its lightweight and easy modification during building the robot.

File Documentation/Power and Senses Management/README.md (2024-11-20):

## Power and Senses Management
### Power Management
The robot is powered by 2 lithium-ion batteries, which are connected to the Raspberry Pi 5. With the help of an uninterruptable power supply that maintains a steady connection between them. The lithium-ion batteries provide us with a reusable power source instead of a traditional battery, which is great as this is more sustainable.

### Sensor Management
**1. RPlidar C1**
The RPLidar C1 is a great alternative to normal sensors (ultrasonics, infrared) as it has the capabilities to take 360-degree samples, which centralize the space for this sensor to one area. This sensor is positioned at the center on top of the Raspberry Pi 5 and is the highest point of the robot.

**2. Light sensor TC01**
This light sensor detects colors on the field to help guide the robot in turning and rounding corners. This sensor is positioned at the bottom of the robot to capture the orange and blue lines that are present at each corner of the arena. If the sensor detects the blue line first, then the robot will make a right turn, and if it detects orange first, then it will make a left turn.

**3. BNO055**
The BNO055 provides multiple features to the robot; it can detect the acceleration of the robot and also its direction as it has a gyro sensor built into it, which helps the robot navigate the arena as it has access to more information on itself. The BNO055 is positioned on top of the Raspberry Pi Pico, which will conserve spaces and ease of connection.

**4. Fish-eye lens camera**
The fish-eye lens camera provides the robot with a wide view of the arena at the front of the robot, which helps in better obstacle detection and recognition. The camera is connected directly to the Raspberry Pi 5 as it's the main processor of the image and is positioned at the front to see the obstacle up ahead of it. The camera is not placed higher in the robot because, in doing so, will hinder the abilities of the RPLidar C1, which is at the top.

## Wiring Diagram

circuit

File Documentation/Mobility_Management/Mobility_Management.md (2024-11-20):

## Mobility Management
### 1. Driving mechanism
The robot uses a steering ackerman to steer the robot left and right. We choose to use this method because it mimics what cars actually use to steer. Due to our freedom to choose how To build our robot, we can choose to build the robot to be as realistic as possible without the limitation that a Lego set will present.[Steering ackerman](https://github.com/user-attachments/assets/70ba4fb7-0aec-4436-890d-90b913467d29)

### 2. Robot Design
The robot is made to be quite short because of our RPLidar C1, which needs to be at the height of the obstacles and walls to be able to detect them; due to this, the robot is not as tall. as other robots. We decided to use traditional car design as the base of our robot as it provide easy visualization on how the movement of the robot and with the 4 wheels we can reduce slippage of wheels. The weight of the robot is mostly concentrated in the middle. because of the placement of the batteries, which resulted in the robot having an ideal center of gravity that will ensure that the robot will not lift off the arena.

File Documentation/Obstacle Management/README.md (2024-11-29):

## Obstacle Management  

### Obstacle Challenge  
In the obstacle challenge, our robot will also needed to complete the requirement as said above, but the robot will also need to avoid additional pillars of green and red that is scatter around the field. The pillars also have it's individual rules that the robot must obey plus a now designated
area for parking the robot.

Obstacle chart

### Parking strategy
We planned to make the robot drive it's back side into the parking area because we design the robot to be long enough so that it can park perfectly within the area without the robot's lenght exceeding the width of the parking zone.

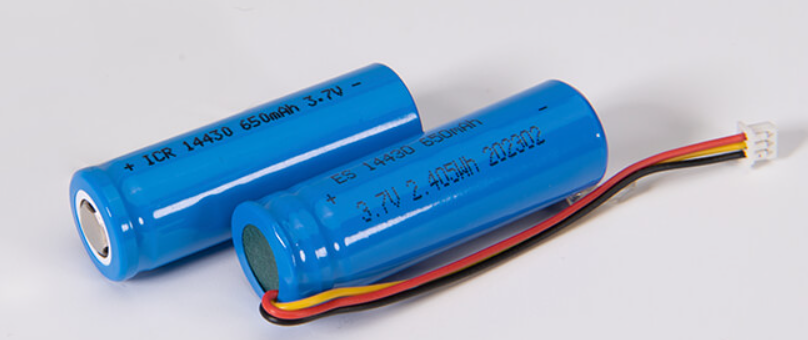
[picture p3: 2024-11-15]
Documentation/Specification/lithium ion batteries.png

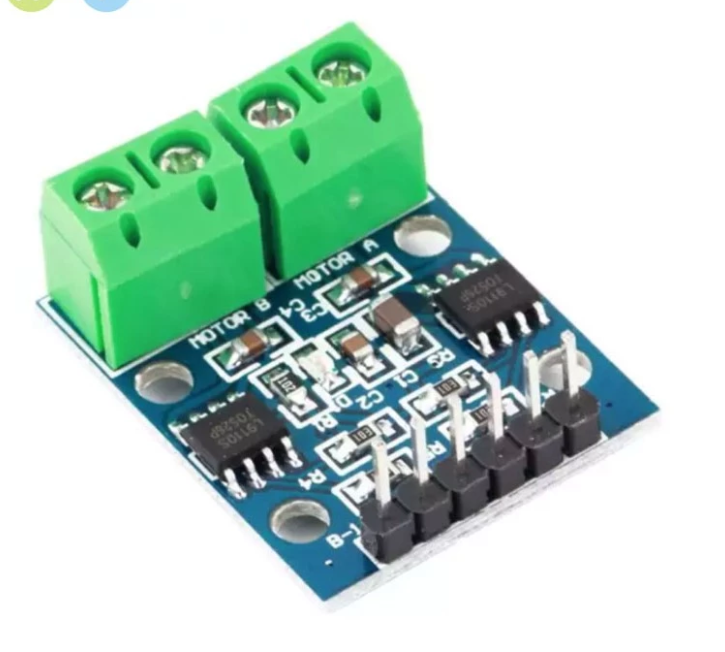
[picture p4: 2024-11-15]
Documentation/Specification/H-bridge.png

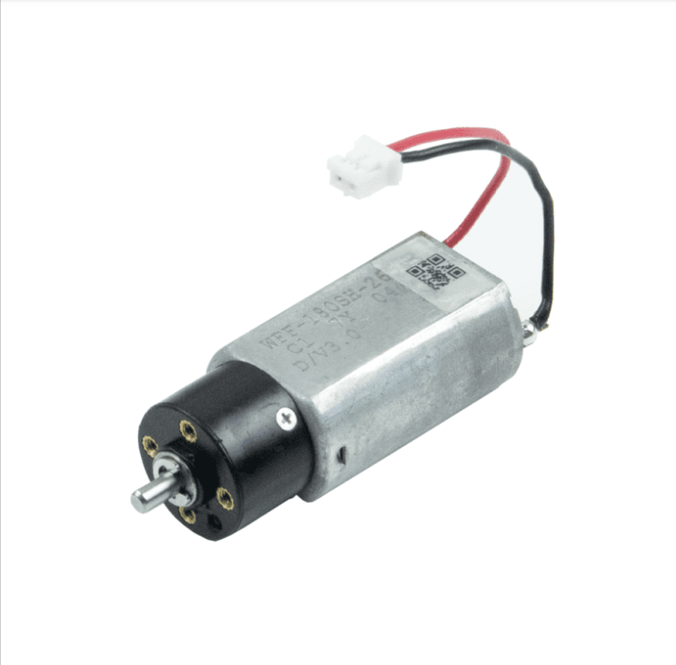
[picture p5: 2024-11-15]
Documentation/Specification/DC gear motor.png

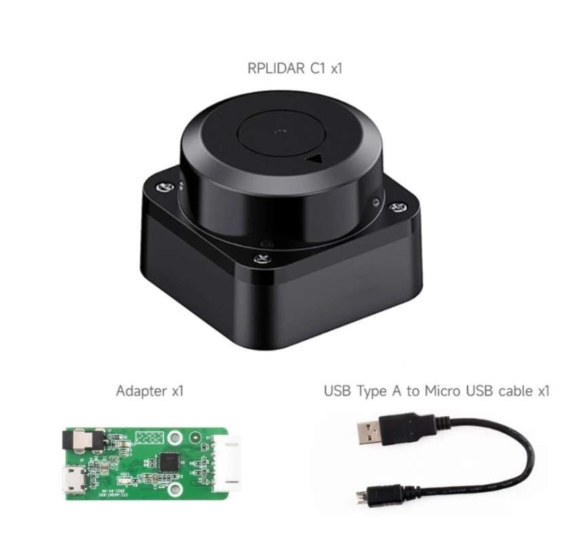
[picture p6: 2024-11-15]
Documentation/Specification/lidar.png

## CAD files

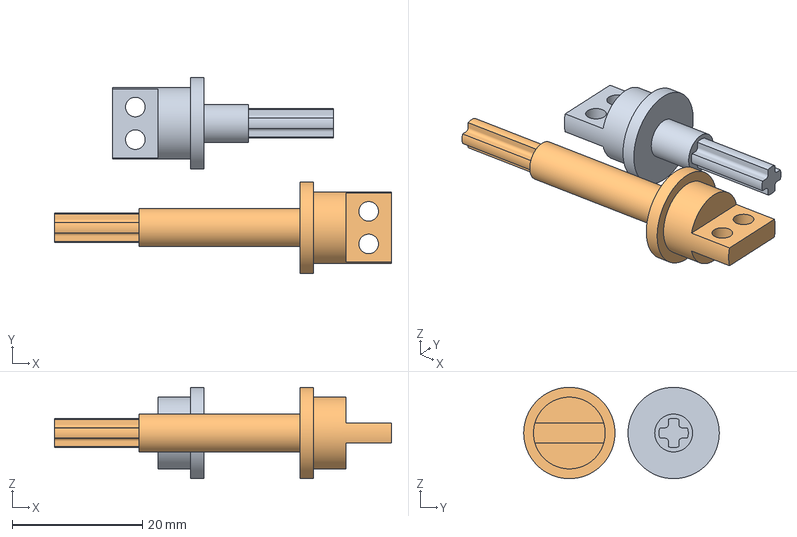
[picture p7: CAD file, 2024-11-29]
Cura-Files/CE3V3KE_BackWheelAxle.3mf
51.7 x 30.0 x 14.0 mm
LeftBackWheelAxle_Export.stl
RightBackWheelAxle_Export.stl

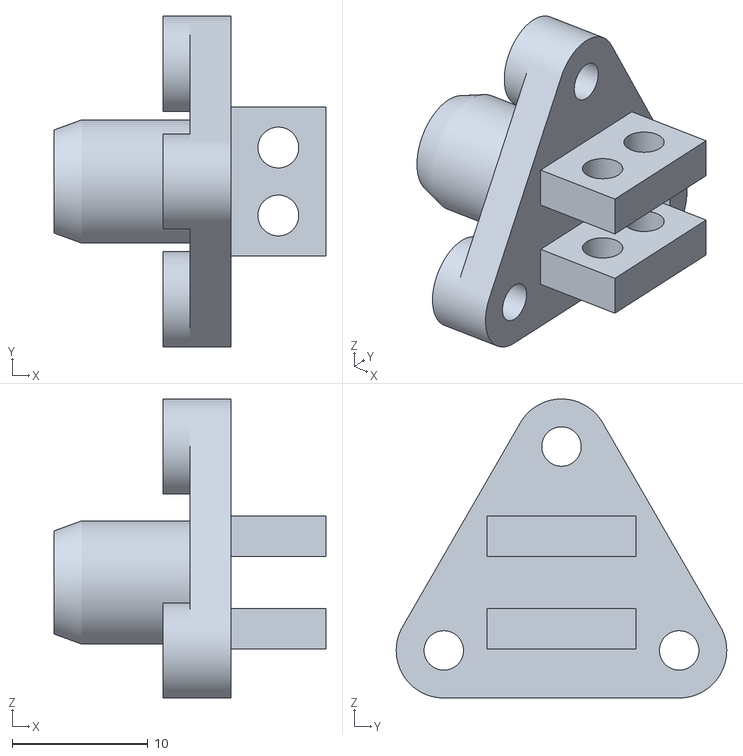
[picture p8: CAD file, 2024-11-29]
STL-Files/BackWheelConnector_2_Export.stl
20.0 x 24.3 x 22.0

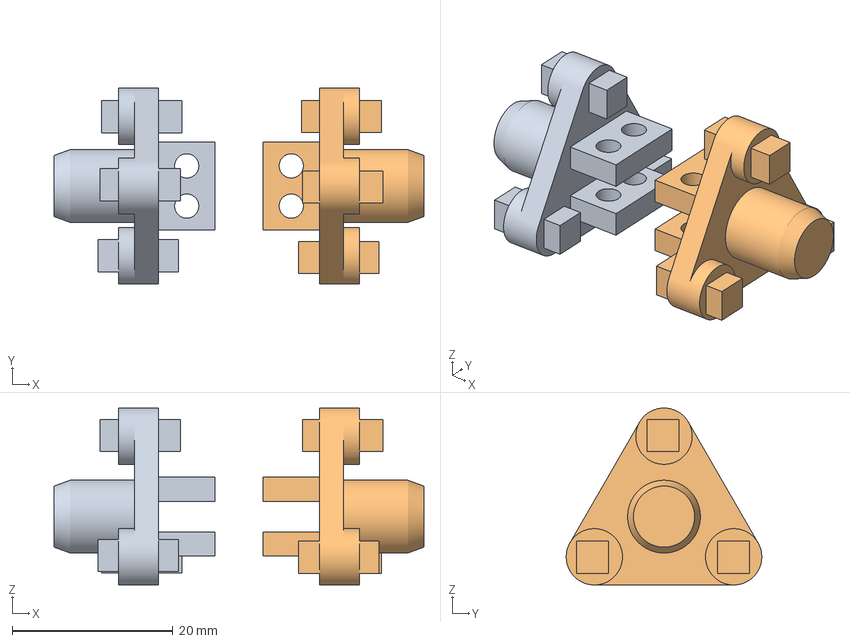
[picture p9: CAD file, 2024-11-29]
Cura-Files/CE3V3KE_BackWheelConnector.3mf
46.0 x 24.3 x 22.0 mm
BackWheelConnector_2_Export.stl
BackWheelConnector_2_Export.stl(1)

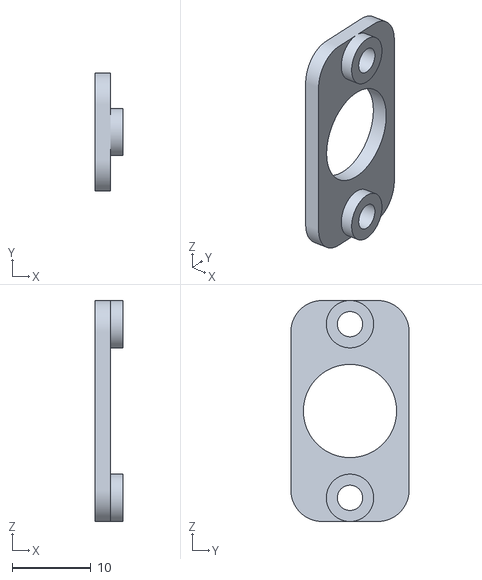
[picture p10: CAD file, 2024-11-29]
STL-Files/BackWheelStopper_2_Export.stl
3.60 x 15.0 x 28.0

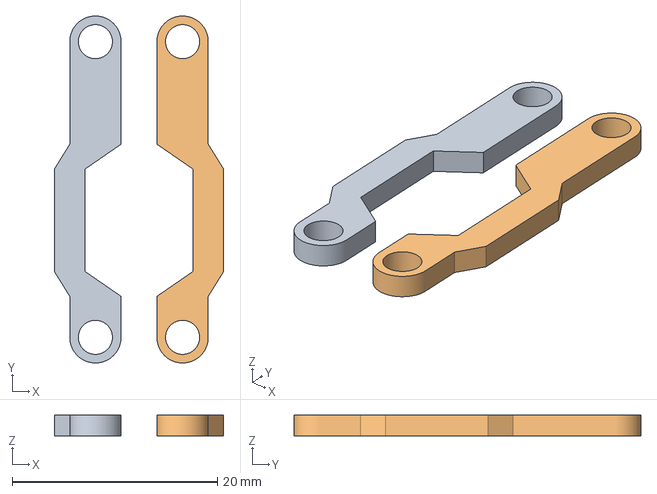
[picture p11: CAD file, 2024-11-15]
Cura-Files/CE3V3KE_TransferLinkage.3mf
16.5 x 33.8 x 2.00 mm
LeftTransferLinkageBody_export(LeftTransferLinkageBody).stl
LeftTransferLinkageBody_export(LeftTransferLinkageBody).stl(1)

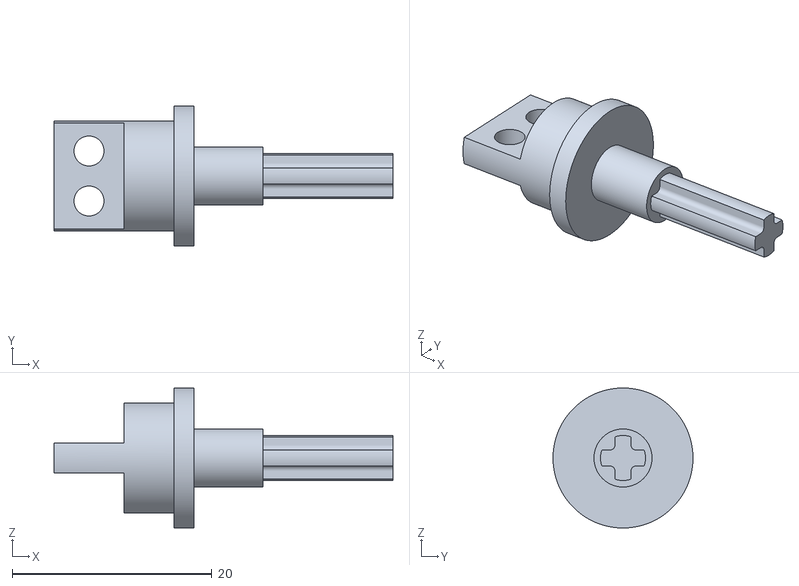
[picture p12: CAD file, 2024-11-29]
STL-Files/LeftBackWheelAxle_Export.stl
33.9 x 14.0 x 14.0

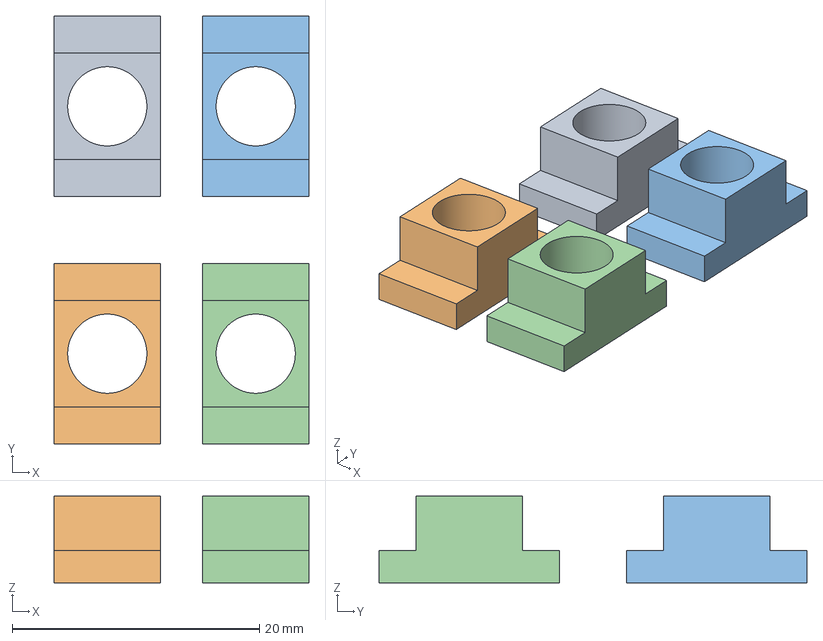
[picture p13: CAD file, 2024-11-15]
Cura-Files/CE3V3KE_AxleHolderBody.3mf
20.6 x 34.6 x 7.00 mm
AxleHolderBody_4_Export.stl
AxleHolderBody_4_Export.stl(1)
AxleHolderBody_4_Export.stl(2)
AxleHolderBody_4_Export.stl(3)

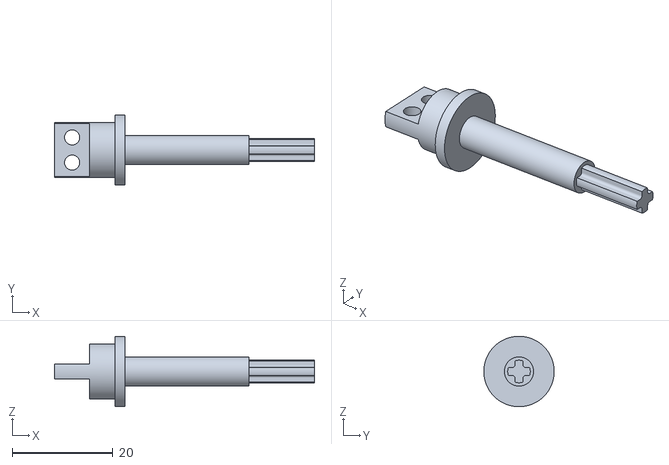
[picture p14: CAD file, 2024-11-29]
STL-Files/RightBackWheelAxle_Export.stl
51.7 x 14.0 x 14.0

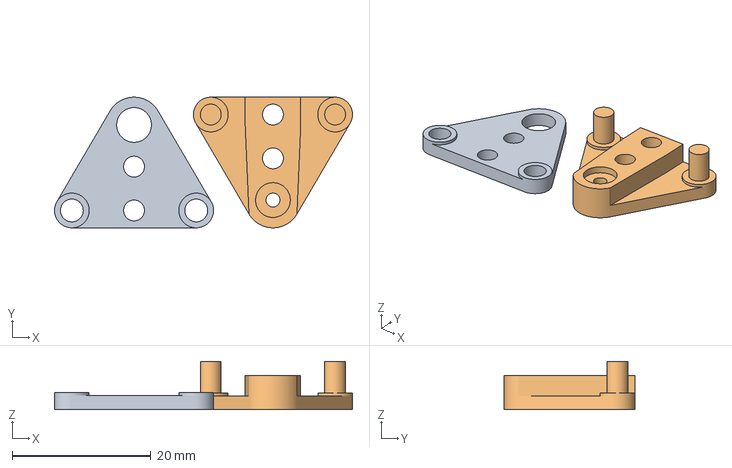
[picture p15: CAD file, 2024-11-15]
Cura-Files/CE3V3KE_TBoneLinkageBody.3mf
42.9 x 18.8 x 6.95 mm
Link001_TopTBoneLinkageBodyBody__export(*TopTBoneLinkageBodyBody).stl
Link_BottomTBoneLinkageBody__export(*BottomTBoneLinkageBody).stl

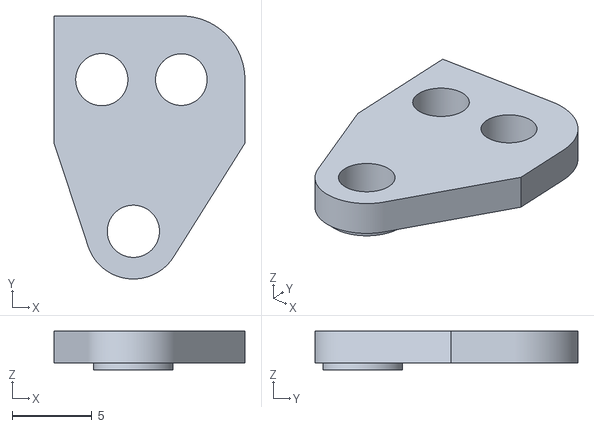
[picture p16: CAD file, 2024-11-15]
STL-Files/TopWheelLinkageBody_M_Export.stl
12.0 x 16.5 x 2.45

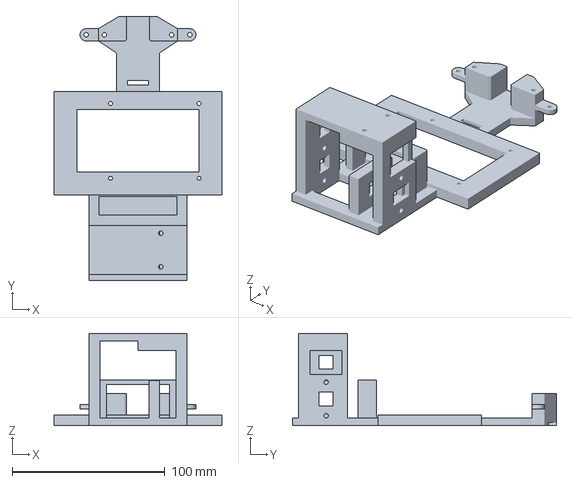
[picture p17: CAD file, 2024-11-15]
Cura-Files/CE3V3KE_BottomChassisBody.3mf
110.0 x 173.0 x 60.5 mm

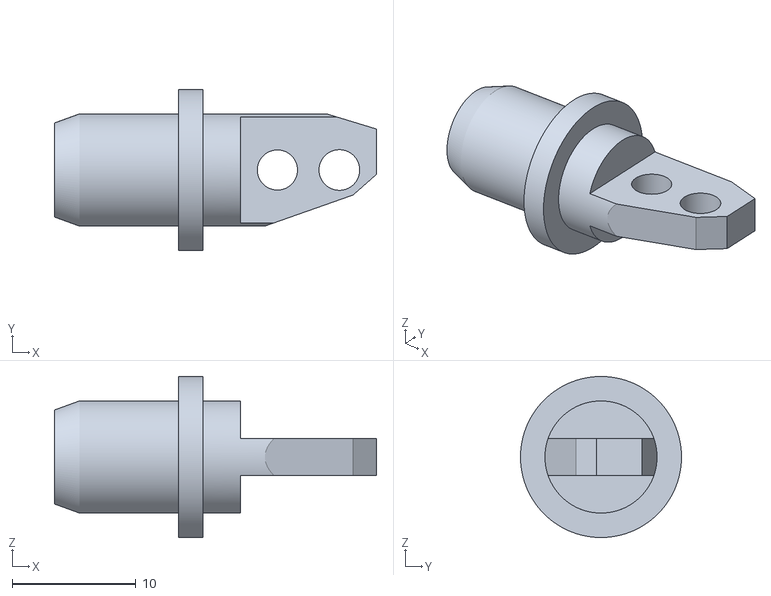
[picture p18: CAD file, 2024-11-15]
STL-Files/WheelAxleBody_M_Export.stl
26.0 x 13.0 x 13.0

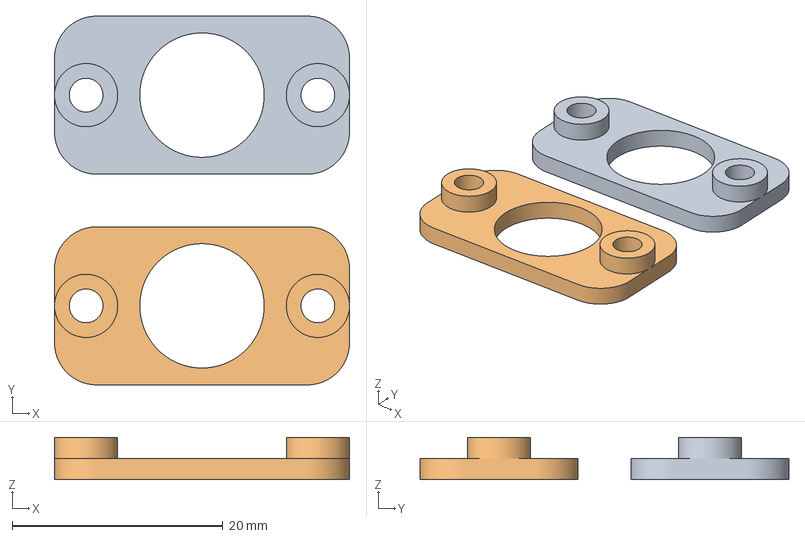
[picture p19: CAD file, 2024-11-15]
Cura-Files/CE3V3KE_BackWheelStopper.3mf
28.0 x 35.0 x 4.00 mm
BackWheelStopper_2_Export.stl
BackWheelStopper_2_Export.stl(1)

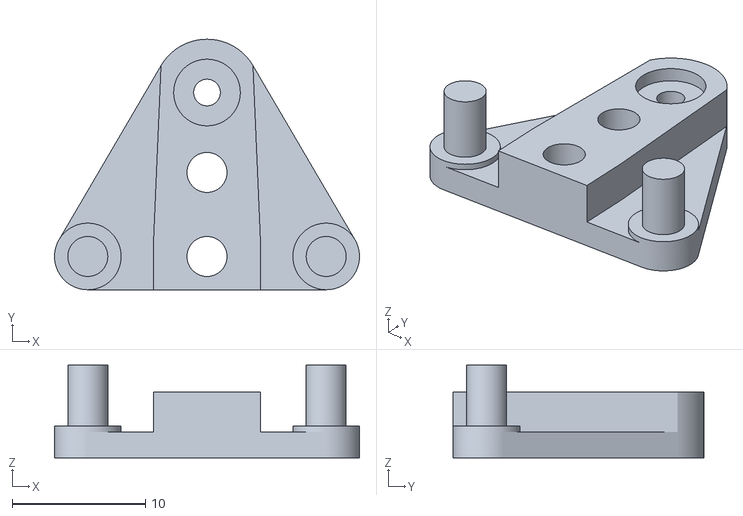
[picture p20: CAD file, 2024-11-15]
STL-Files/BottomTBoneLinkageBody_Export.stl
22.9 x 18.8 x 6.95

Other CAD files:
Cura-Files/CE3V3KE_MotorHolder.3mf
STL-Files/AxleHolderBody_4_Export.stl
Cura-Files/CE3V3KE_TopChassisBody.3mf
STL-Files/LeftTransferLinkageBody_Export.stl
Cura-Files/CE3V3KE_LidarHolder.3mf
Cura-Files/CE3V3KE_WheelLinakage.3mf
Cura-Files/CE3V3KE_WheelStopper.3mf
STL-Files/BottomChassisBody_Export.stl
STL-Files/BottomWheelLinkageBody_M_Export.stl
STL-Files/MotorHolder_Export.stl
STL-Files/RightTransferLinkageBody_Export.stl
STL-Files/TopChassisBody_Export.stl
STL-Files/TopTBoneLinkageBodyBody_Export.stl
STL-Files/WheelStopperBody_M_Export.stl

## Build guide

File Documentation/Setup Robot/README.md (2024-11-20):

## Printing
- Downloaded the [3D Cura files](https://github.com/Chayanon-Ninyawee/KMIDS-TDF-WRO-Future-Engineers-2024/tree/402e0bc6fe819bc5726d7b25003a4c2b3e62147d/Cura-Files) for printing
- Use PLA as your material
- Print all the parts from Creality Ender-3 V3

## Assembling
When assembling the robot, you can generally follow how it is assemble in our [3D model](https://github.com/Chayanon-Ninyawee/KMIDS-TDF-WRO-Future-Engineers-2024/tree/402e0bc6fe819bc5726d7b25003a4c2b3e62147d/KMIDS-TDF-WRO2024-FreeCAD) but some parts require additional note when assembling.

### Back Wheels
When assembling the back wheels, it is recommended that you have a screwdriver with you when installing the back wheel stopper. The back wheel stopper needed to have something preventing it from screwing towards the body. We inserted the screwdriver between them and then screwed in the screw; this made sure that the stopper would not be too tight and prevent the back wheels from spinning freely.

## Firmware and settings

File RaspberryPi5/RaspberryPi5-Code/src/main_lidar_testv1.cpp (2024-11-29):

#include <chrono>
#include <cmath>
#include <csignal>
#include <iostream>
#include <opencv2/opencv.hpp>
#include <thread>
#include <vector>

#include "utils/i2c_master.h"
#include "utils/lidarController.h"
#include "utils/lidarDataProcessor.h"
#include "utils/lccv.hpp"
#include "utils/imageProcessor.h"
#include "utils/dataSaver.h"

const uint8_t PICO_ADDRESS = 0x39;

const int LIDAR_WIDTH = 1200;
const int LIDAR_HEIGHT = 1200;
const float LIDAR_SCALE = 180.0;

const cv::Point CENTER(LIDAR_WIDTH/2, LIDAR_HEIGHT/2);

uint32_t camWidth = 648;
uint32_t camHeight = 486;


float motorPercent = 0.0f;
float steeringPercent = 0.0f;


bool isRunning = true;







// Global variable to store the clicked point coordinates
cv::Point clickPoint(-1, -1);

// Mouse callback function to capture the click event
void onMouse(int event, int x, int y, int flags, void* userdata) {
    if (event == cv::EVENT_LBUTTONDOWN) {
        // Store the clicked point
        clickPoint = cv::Point(x, y);
    }
}






void drawRadialLines(cv::Mat &image, const cv::Point &center, float angle, int length, cv::Scalar color, int thickness = 1) {
    // Convert angle to radians
    double theta = angle * CV_PI / 180.0;

    // Calculate the end point of the line
    int endX = static_cast<int>(center.x + length * std::sin(theta));
    int endY = static_cast<int>(center.y - length * std::cos(theta));

    // Draw the line from the center to the end point
    cv::line(image, center, cv::Point(endX, endY), color, thickness);
}







void interuptHandler(int signum) {
    isRunning = false;
}


int main(int argc, char **argv) {
    signal(SIGINT, interuptHandler);



    // Set up camera

    lccv::PiCamera cam;
    cam.options->video_width = camWidth;
    cam.options->video_height = camHeight;
    cam.options->framerate = 30; // Increase frame rate for reduced blur
    cam.options->brightness = 0.2;
    cam.options->contrast = 1.0;
    cam.options->shutter = 10000; // Set shutter speed to 500 µs (adjust as needed)
    cam.options->gain = 10.0; // Increase gain for brightness compensation
    cam.options->setExposureMode(Exposure_Modes::EXPOSURE_SHORT);
    cam.options->verbose = true;
    cam.startVideo();







    // Set up Raspberry Pi Pico I2C

    int fd = i2c_master_init(PICO_ADDRESS);

    i2c_master_send_command(fd, Command::RESTART);
    std::this_thread::sleep_for(std::chrono::milliseconds(100));


    i2c_master_send_command(fd, Command::SKIP_CALIB);

    // uint8_t calib[22];
    // bool isCalibDataExist = DataSaver::loadData("config/calibData.bin", calib);

    // if (isCalibDataExist) {
    //     i2c_master_send_data(fd, i2c_slave_mem_addr::BNO055_CALIB_ADDR, calib, sizeof(calib));
    //     i2c_master_send_command(fd, Command::CALIB_WITH_OFFSET);
    // } else {
    //     i2c_master_send_command(fd, Command::CALIB_NO_OFFSET);
    // }

    uint8_t status[i2c_slave_mem_addr::STATUS_SIZE] = {0};
    uint8_t logs[i2c_slave_mem_addr::LOGS_BUFFER_SIZE] = {0};
    while (not(status[0] & (1 << 1))) {
        i2c_master_read_status(fd, status);

        i2c_master_read_logs(fd, logs);
        i2c_master_print_logs(logs, sizeof(logs));

        std::this_thread::sleep_for(std::chrono::milliseconds(50));
    }

    // uint8_t new_calib[22];
    // i2c_master_read_bno055_calibration(fd, new_calib);

    // DataSaver::saveData("config/calibData.bin", new_calib, false);

    // for (int i = 0; i < sizeof(new_calib); i++) {
    //     printf("%x, ", new_calib[i]);
    // }
    // printf("\n");

    i2c_master_send_command(fd, Command::NO_COMMAND);
    std::this_thread::sleep_for(std::chrono::milliseconds(20));








    // Set up Lidar

    lidarController::LidarController lidar;
    if (!lidar.initialize() || !lidar.startScanning()) {
        return -1;
    }






    cv::namedWindow("LIDAR Hough Lines", cv::WINDOW_AUTOSIZE);
    cv::setMouseCallback("LIDAR Hough Lines", onMouse);




    printf("Press Any Key to Start\n");  
    getchar();





    bno055_accel_float_t initialAccelData;
    bno055_euler_float_t initialEulerData;
    i2c_master_read_bno055_accel_and_euler(fd, &initialAccelData, &initialEulerData);







    int64 start = cv::getTickCount();
    while (isRunning) {
        cv::Mat rawCameraImage;
        if(!cam.getVideoFrame(rawCameraImage, 1000)){
            std::cout<<"Timeout error"<<std::endl;
        }
        cv::Mat cameraImage;
        cv::flip(rawCameraImage, cameraImage, -1);


        bno055_accel_float_t accelData;
        bno055_euler_float_t eulerData;
        i2c_master_read_bno055_accel_and_euler(fd, &accelData, &eulerData);

        i2c_master_read_logs(fd, logs);
        i2c_master_print_logs(logs, sizeof(logs));




        auto lidarScanData = lidar.getScanData();
        // lidar.printScanData(lidarScanData);

        cv::Mat binaryImage = lidarDataToImage(lidarScanData, LIDAR_WIDTH, LIDAR_HEIGHT, LIDAR_SCALE);
        cv::Mat lidarOutputImage = cv::Mat::zeros(LIDAR_HEIGHT, LIDAR_WIDTH, CV_8UC3);
        cv::cvtColor(binaryImage, lidarOutputImage, cv::COLOR_GRAY2BGR);



        // auto angle = fmod(eulerData.h - initialEulerData.h + 360.0f, 360.0f);
        float angle = 0.0;



        auto lines = detectLines(binaryImage);
        auto combinedLines = combineAlignedLines(lines);
        auto wallDirections = analyzeWallDirection(combinedLines, angle, CENTER);

        drawAllLines(lidarOutputImage, combinedLines, wallDirections);




        Direction direction = NORTH;
        if (angle >= 337.5 || angle < 22.5) direction = NORTH;
        else if (angle >= 22.5 && angle < 112.5) direction = EAST;
        else if (angle >= 112.5 && angle < 202.5) direction = SOUTH;
        else if (angle >= 202.5 && angle < 292.5) direction = WEST;




        auto trafficLightPoints = detectTrafficLight(binaryImage, combinedLines, wallDirections, COUNTER_CLOCKWISE, direction);




        for (const auto point : trafficLightPoints) {
            cv::circle(lidarOutputImage, point, 5, cv::Scalar(255, 120, 255), cv::FILLED);
        }

        cv::circle(lidarOutputImage, CENTER, 10, cv::Scalar(0, 120, 255), cv::FILLED);

        // cv::Mat filteredCameraImage = filterAllColors(cameraImage);
        auto cameraImageData = processImage(cameraImage);
        auto filteredImage = filterAllColors(cameraImage);
        cv::Mat processedImage = drawImageProcessingResult(cameraImageData, cameraImage);

        
        std::vector<BlockInfo> blockAngles;
        for (Block block : cameraImageData.blocks) {
            BlockInfo blockAngle;
            blockAngle.angle = pixelToAngle(block.x, camWidth, 20, 88.0f);
            blockAngle.size = block.size;
            blockAngle.color = block.color;
            blockAngles.push_back(blockAngle);
            
            // cv::Scalar color;
            // if (blockAngle.color == RED) {
            //     color = cv::Scalar(0, 0, 255);
            // } else {
            //     color = cv::Scalar(0, 255, 0);
            // }

            // drawRadialLines(lidarOutputImage, CENTER, blockAngle.angle, 800, color, 2);
        }
        auto processedTrafficLights = processTrafficLight(trafficLightPoints, blockAngles, CENTER);

        drawTrafficLights(lidarOutputImage, processedTrafficLights);


        cv::imshow("LIDAR Hough Lines", processedImage);




        // Check if a mouse click was detected
        if (clickPoint.x != -1 && clickPoint.y != -1) {
            // Get the pixel color at the clicked point (in BGR format)
            cv::Vec3b pixelColor = cameraImage.at<cv::Vec3b>(clickPoint);

            // Convert the BGR color to HSV
            cv::Mat hsvImage;
            cv::cvtColor(cameraImage, hsvImage, cv::COLOR_BGR2HSV);
            cv::Vec3b hsvColor = hsvImage.at<cv::Vec3b>(clickPoint);

            // Print the HSV values
            std::cout << "HSV of clicked pixel (" << clickPoint.x << ", " << clickPoint.y << "): "
                      << "H = " << (int)hsvColor[0] << ", "
                      << "S = " << (int)hsvColor[1] << ", "
                      << "V = " << (int)hsvColor[2] << std::endl;

            // Reset the clickPoint
            clickPoint = cv::Point(-1, -1);
        }





        uint8_t movement[sizeof(motorPercent) + sizeof(steeringPercent)];

        memcpy(movement, &motorPercent, sizeof(motorPercent));
        memcpy(movement + sizeof(motorPercent), &steeringPercent, sizeof(steeringPercent));
        i2c_master_send_data(fd, i2c_slave_mem_addr::MOVEMENT_INFO_ADDR, movement, sizeof(movement));


        char key = cv::waitKey(1);
        if (key == 'q') {
            break;
        }

        int64 end = cv::getTickCount();
        double duration = (end - start) / cv::getTickFrequency();
        double fps = 1.0 / duration;
        // printf("FPS: %.3f, # of lines: %d\n", fps, combinedLines.size());

        start = cv::getTickCount();
    }

    cam.stopVideo();

    lidar.shutdown();
    cv::destroyAllWindows();

    return 0;
}

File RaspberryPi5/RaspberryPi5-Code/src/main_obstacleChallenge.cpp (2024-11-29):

#include <chrono>
#include <cmath>
#include <csignal>
#include <iostream>
#include <opencv2/opencv.hpp>
#include <opencv2/imgproc.hpp>
#include <opencv2/core.hpp>
#include <opencv2/imgcodecs.hpp>
#include <opencv2/highgui.hpp>
#include <thread>
#include <vector>
#include <wiringPi.h>

#include "challenges/obstacleChallenge.h"

#include "utils/i2c_master.h"
#include "utils/lccv.hpp"
#include "utils/lidarController.h"
#include "utils/lidarDataProcessor.h"
#include "utils/dataSaver.h"

const int BUTTON_PIN = 23;
const uint8_t PICO_ADDRESS = 0x39;

float motorPercent = 0.0f;
float steeringPercent = 0.0f;


const int WIDTH = 1200;
const int HEIGHT = 1200;
const float LIDAR_SCALE = 180.0;

const cv::Point CENTER(WIDTH/2, HEIGHT/2);


uint32_t camWidth = 1296;
uint32_t camHeight = 972;


float lastGyroYaw = 0.0f;
float accumulateGyroYaw = 0.0f;

bool isRunning = true;

void interuptHandler(int signum) {
    isRunning = false;
}


// Draw all lines with different colors based on direction (NORTH, EAST, SOUTH, WEST)
void drawAllLines(const std::vector<cv::Vec4i> &lines, cv::Mat &outputImage, double gyroYaw) {
    // Analyze the direction of each wall using the analyzeWallDirection function
    std::vector<Direction> wallDirections = analyzeWallDirection(lines, gyroYaw, CENTER);

    for (size_t i = 0; i < lines.size(); ++i) {
        cv::Vec4i line = lines[i];
        Direction direction = wallDirections[i];  // Get the direction of the current line

        // Determine the color based on the direction
        cv::Scalar color;
        if (direction == NORTH) {
            color = cv::Scalar(0, 0, 255); // Red for NORTH
        } else if (direction == EAST) {
            color = cv::Scalar(0, 255, 0); // Green for EAST
        } else if (direction == SOUTH) {
            color = cv::Scalar(255, 0, 0); // Blue for SOUTH
        } else if (direction == WEST) {
            color = cv::Scalar(255, 255, 0); // Yellow for WEST
        }

        // Draw the line with the determined color
        cv::line(outputImage, cv::Point(line[0], line[1]), cv::Point(line[2], line[3]), color, 2, cv::LINE_AA);
    }
}


int main() {
    signal(SIGINT, interuptHandler);

    std::time_t now = std::time(nullptr);
    std::tm localTime;
    localtime_r(&now, &localTime); // Use `localtime_r` for thread-safe conversion

    std::ostringstream timestampStream;
    timestampStream << std::put_time(&localTime, "%Y%m%d_%H%M%S"); // Format: YYYYMMDD_HHMMSS
    std::string timestamp = timestampStream.str();

    // cv::namedWindow("LIDAR Hough Lines", cv::WINDOW_AUTOSIZE);


    lccv::PiCamera cam;
    cam.options->video_width = camWidth;
    cam.options->video_height = camHeight;
    cam.options->framerate = 30; // Increase frame rate for reduced blur
    cam.options->brightness = 0.2;
    cam.options->contrast = 1.0;
    cam.options->shutter = 10000; // Set shutter speed to 500 µs (adjust as needed)
    cam.options->gain = 10.0; // Increase gain for brightness compensation
    cam.options->setExposureMode(Exposure_Modes::EXPOSURE_SHORT);
    // cam.options->setWhiteBalance(WhiteBalance_Modes::WB_DAYLIGHT);
    cam.options->verbose = true;
    cam.startVideo();


    if (wiringPiSetupGpio() == -1) { // Use GPIO numbering
        printf("WiringPi setup failed.\n");
        return -1;
    }

    // Set up GPIO 23 as input with pull-up resistor
    pinMode(BUTTON_PIN, INPUT);
    pullUpDnControl(BUTTON_PIN, PUD_UP); // Enable pull-up resistor


    int fd = i2c_master_init(PICO_ADDRESS);

    uint8_t logs[i2c_slave_mem_addr::LOGS_BUFFER_SIZE] = {0};

    i2c_master_send_command(fd, Command::RESTART);
    std::this_thread::sleep_for(std::chrono::milliseconds(100));



    uint8_t calib[22];
    bool isCalibDataExist = DataSaver::loadData("config/calibData.bin", calib);

    // if (isCalibDataExist) {
    //     i2c_master_send_data(fd, i2c_slave_mem_addr::BNO055_CALIB_ADDR, calib, sizeof(calib));
    //     i2c_master_send_command(fd, Command::CALIB_WITH_OFFSET);
    // } else {
    //     i2c_master_send_command(fd, Command::CALIB_NO_OFFSET);
    // }
    i2c_master_send_command(fd, Command::SKIP_CALIB);

    std::this_thread::sleep_for(std::chrono::milliseconds(100));

    uint8_t status[i2c_slave_mem_addr::STATUS_SIZE] = {0};
    while (not(status[0] & (1 << 1))) {
        i2c_master_read_status(fd, status);

        i2c_master_read_logs(fd, logs);
        i2c_master_print_logs(logs, sizeof(logs));

        std::this_thread::sleep_for(std::chrono::milliseconds(50));
    }

    // uint8_t new_calib[22];
    // i2c_master_read_bno055_calibration(fd, new_calib);

    // DataSaver::saveData("config/calibData.bin", new_calib, false);

    // for (int i = 0; i < sizeof(new_calib); i++) {
    //     printf("%x, ", new_calib[i]);
    // }
    // printf("\n");



    i2c_master_send_command(fd, Command::NO_COMMAND);
    std::this_thread::sleep_for(std::chrono::milliseconds(20));


    lidarController::LidarController lidar;
    if (!lidar.initialize() || !lidar.startScanning()) {
        return -1;
    }

    while (digitalRead(BUTTON_PIN) == HIGH) {
        delay(10); // Small delay to reduce CPU usage
    }
    delay(500);

    bno055_accel_float_t initial_accel_data;
    bno055_euler_float_t initial_euler_data;
    i2c_master_read_bno055_accel_and_euler(fd, &initial_accel_data, &initial_euler_data);

    lastGyroYaw = initial_euler_data.h;

    ObstacleChallenge challenge = ObstacleChallenge(LIDAR_SCALE, CENTER);


    while (isRunning) {
        cv::Mat rawCameraImage;
        if(!cam.getVideoFrame(rawCameraImage, 1000)){
            std::cout<<"Timeout error"<<std::endl;
        }
        cv::Mat cameraImage;
        cv::flip(rawCameraImage, cameraImage, -1);
 


        bno055_accel_float_t accel_data;
        bno055_euler_float_t euler_data;
        i2c_master_read_bno055_accel_and_euler(fd, &accel_data, &euler_data);

        float deltaYaw = euler_data.h - lastGyroYaw;
        if (deltaYaw > 180.0f) {
            deltaYaw -= 360.0f;
        } else if (deltaYaw < -180.0f) {
            deltaYaw += 360.0f;
        }
        accumulateGyroYaw += deltaYaw;
        lastGyroYaw = euler_data.h;

        // printf("accumulateGyroYaw: %.2f, test: %.2f, ", accumulateGyroYaw, fmod(accumulateGyroYaw*1.007274762 + 360.0f*20, 360.0f));


        i2c_master_read_logs(fd, logs);
        i2c_master_print_logs(logs, sizeof(logs));

        auto lidarScanData = lidar.getScanData();
        cv::Mat binaryImage = lidarDataToImage(lidarScanData, WIDTH, HEIGHT, LIDAR_SCALE);

        challenge.update(binaryImage, cameraImage, fmod(accumulateGyroYaw*1.0065+ 360.0f*20, 360.0f), motorPercent, steeringPercent);
        steeringPercent = std::clamp(steeringPercent, -1.0f, 1.0f);
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

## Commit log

2024-05-27 Removed Servo Additional Arms
    [Car_Assembly.0025.iam, Car_Assembly.0026.iam, Car_Assembly.iam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]
2024-06-02 New Steering Linkage, Cleanup Car_Plan, Done Connecting Servo
    [Car_Assembly.0026.iam, Car_Assembly.0053.iam, Car_Assembly.iam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]
2024-06-02 Added Camera to Front Bridge
    [Car_Assembly.0054.iam, Car_Assembly.0056.iam, Car_Assembly.iam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]
2024-06-02 Add lower chassis with lego frame connector
    [4519 DkStone Technic Axle 3.0002.ipt, 4519 DkStone Technic Axle 3.ipt, Car_Assembly.0056.iam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]
2024-06-03 connected motor to driving shaft and lower chassis
    [Car_Assembly.0066.iam, Car_Assembly.0069.iam, Car_Assembly.iam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]
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2024-06-03 connected wheels the the lego axles
    [Car_Assembly.0070.iam, Car_Assembly.0074.iam, Car_Assembly.iam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]
2024-06-03 Added camera support and Fixed servo screw
    [Car_Assembly.0074.iam, Car_Assembly.0076.iam, Car_Assembly.iam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]
2024-06-03 Added screw for higher floor in Lower Chassis
    [Car_Assembly.0076.iam, Car_Assembly.0077.iam, Car_Assembly.iam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]
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2024-06-04 Added screw to secure the Lego Frames
    [Car_Assembly.0078.iam, Car_Assembly.0079.iam, Car_Assembly.iam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]
2024-06-05 Created STL Files for parts use in Front Bridge and imported them to Cura
    [Front_Bridge.stl, Front_Part.3mf, Front_Wheel_Anchor.stl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]
2024-06-06 Front_Wheel_Anchor
    fixed front wheel anchor
    [Front_Wheel_Anchor.0030.ipt, Front_Wheel_Anchor.0031.ipt, Front_Wheel_Anchor.ipt]
2024-06-06 Fixed Front Bridge
    [Front_Bridge.0072.ipt, Front_Bridge.0077.ipt, Front_Bridge.ipt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]
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2024-06-06 commit for merging with latest commit in main
    [Car_Assembly.0079.iam, Car_Assembly.0082.iam, Car_Assembly.iam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]
2024-06-06 fix merge conflict
    [Lower_Chassis.ipt]
2024-06-06 Done Fixing Car Assembly
    [CE3PRO_Front_Part.3mf, CE3PRO_Lower_Chassis.3mf, Car_Assembly.0082.iam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]
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2024-06-07 Added clearance
    [CE3PRO_Front_Part.3mf, CE3PRO_Lower_Chassis.3mf, Car_Assembly.0090.iam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]
2024-06-09 Fixed Clearance and changed 3D printer profile
    [CE3E3V2_Front_Bridge.3mf, CE3E3V2_Lower_Chassis.3mf, CE3E3V2_Misc.3mf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]
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2024-06-10 Added Front_bridge clearance
    [CE3E3V2_Front_Bridge.3mf, Front_Bridge.0087.ipt, Front_Bridge.0089.ipt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]
2024-06-10 change wall thickness to 3mm
    [Front_Wheel_Anchor.0047.ipt, Front_Wheel_Anchor.0048.ipt, Front_Wheel_Anchor.ipt]
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2024-06-11 Changed Lower_Chassis clearance
    [CE3E3V2_Lower_Chassis.3mf, Car_Assembly.0098.iam, Car_Assembly.0100.iam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]
2024-06-12 Added Ultrasonic Sensor to Car_Assembly
    [CE3E3V2_Motor_Lego_Axle_Connector.3mf, Car_Assembly.0100.iam, Car_Assembly.0101.iam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]
2024-06-12 cura make lower chasis easier to remove
    [CE3E3V2_Lower_Chassis.3mf]
2024-06-12 Added Ultrasonic Sensor to Front_Bridge
    [Car_Assembly.0101.iam, Car_Assembly.0105.iam, Car_Assembly.iam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]
2024-06-12 Created Cura for Front Bridges
    [CE3E3V2_Front_Bridge.3mf]
2024-06-13 Added 1.5_Base to Car_Assembly
    [Car_Assembly.0105.iam, Car_Assembly.0113.iam, Car_Assembly.iam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]
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2024-06-13 Created STL Files for Lower_Chassis
    [Car_Assembly.0114.iam, Car_Assembly.0116.iam, Car_Assembly.iam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]
2024-06-13 Added sensors and Raspberry Pi 5 to Car_Assembly
    [1.5_base.0001.ipt, 1.5_base.0004.ipt, 1.5_base.ipt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]
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2024-06-13 Created STL Files for every changes and change Cura settings for Lower_Chassis
    [CE3E3V2_Front_Bridge.3mf, CE3E3V2_Lower_Chassis.3mf, Car_Assembly.0127.iam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]
2024-06-13 Added Arduino Nano to Car_Assembly
    [102 RESISTOR PACK.ipt, 15pin_header__.ipt, 16mhz crystal - measured.ipt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]
2024-06-13 Created Cura files for all small parts
    [CE3E3V2_Lego_Frame_Holder.3mf, CE3E3V2_Lego_Frame_Holder_Extra_2.3mf, CE3E3V2_Servo_Steering_Linkage.3mf]
2024-06-28 frontBridge-ultraSensor
    widen gap in the front bridge for ultrasonic sensor
    [Car_Assembly.0132.iam, Front_Bridge.0121.ipt, Front_Bridge.0122.ipt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]
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2024-06-30 Renamed STL Files to Ender_3_V3_STL_and_Slicer_Files
    [1.5_base.stl, Front_Bridge.stl, Front_Bridge_2.stl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]
2024-06-30 Changed clearance to fit with Ender 3 V3 KE printer
    [Front_Bridge.0123.ipt, Front_Bridge.0125.ipt, Front_Bridge.ipt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]
2024-06-30 Created STL Files for the changed parts
    [Front_Bridge.0125.ipt, Front_Bridge.0127.ipt, Front_Bridge.ipt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]
2024-06-30 Change Front_Bridge so it fit M3 instead of M2
    [Front_Bridge.0127.ipt, Front_Bridge.0130.ipt, Front_Bridge.ipt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]
2024-06-30 Changed Front_Bridge so that camera fit
    [Car_Assembly.0145.iam, Front_Bridge.0130.ipt, Front_Bridge.0133.ipt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]
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2024-06-30 Changed Steering System so that it turn better
    [1.5_base.0043.ipt, 1.5_base.0045.ipt, 1.5_base.ipt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]
2024-06-30 Exported new Steering System to STL
    [Front_Bridge.0137.ipt, Front_Bridge.0141.ipt, Front_Bridge.ipt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]
2024-06-30 Changed M3 and M4 clearance in Steering System
    [Front_Bridge.0141.ipt, Front_Bridge.0143.ipt, Front_Bridge.ipt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]
2024-06-30 Added hex nut to prevent front wheel from swiveling
    [Front_Bridge.0143.ipt, Front_Bridge.0145.ipt, Front_Bridge.ipt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]
2024-07-03 Seperated Wheel_Lego_Axle_Connector into 2 part
    [Wheel_Lego_Axle_Connector.0003.ipt, Wheel_Lego_Axle_Connector.0010.ipt, Wheel_Lego_Axle_Connector.ipt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]
2024-07-03 Changed clearance
    [1.5_base.stl, 2_Base.stl, Car_Assembly.0191.iam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]
2024-07-08 Added Game_Mat to the simulator
    [1.5_base.0045.ipt, 1.5_base.0050.ipt, 1.5_base.ipt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]
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2024-07-24 Move motor so that the axle align with the center of the car
    [Lower_Chassis.0088.ipt, Lower_Chassis.0089.ipt, Lower_Chassis.ipt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]
2024-07-27 Make differential gear better
    [Lower_Chassis.0089.ipt, Lower_Chassis.0114.ipt, Lower_Chassis.ipt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]
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2024-08-02 Update README.md
    - Add the rest of the description for the electronice
    - fix the wiring diagram to include a servo
2024-08-02 fix flowcharts
2024-08-03 Lower_Chassis snapping problem fix
    [Lower_Chassis.0118.ipt, Lower_Chassis.0120.ipt, Lower_Chassis.ipt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]
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2024-08-15 Fix front_bridge
    [Car_Assembly.0208.iam, Front_Bridge.0173.ipt, Front_Bridge.0175.ipt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]
2024-08-15 Fix 1.5_base
    [1.5_base.0061.ipt, 1.5_base.0062.ipt, 1.5_base.ipt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]
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2024-09-29 Fix Wheel
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2024-09-30 Change clearance name and Add clearance to wheel linkage
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2024-10-01 Add Steering System TODO: Fix Transfer Linkage
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2024-10-06 Import Lego Differential Gear
    [LegoDiffGear.FCStd]
2024-10-06 Make LegoDiffGear use shape instead of mesh
    [LegoDiffGear.FCStd]
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2024-10-08 Use 24-16 LegoDiffGear instead of the Bevel LegoDiffGear
    [LegoDiffGear.FCStd]
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2024-10-10 Fix BackWheel Dimension issue and assemble everything in SteeringSystem
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2024-10-14 Export all printed part to STL
    [AxleHolderBody_export(AxleHolderBody).stl, BackWheelAxle_export(BackWheelAxle).stl, BackWheelConnector_export(BackWheelConnector).stl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]
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2024-10-14 Fix BottomChassis Tip not at the end and re-export the STL
    [BottomChassisBody_export(BottomChassisBody).stl, CE3V3KE_BottomChassisBody.3mf, MotorHolder_export.xml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]
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2024-10-17 Make BottomChassis able to fit large motor
    [AxleHolderBody_4_Export.stl, AxleHolderBody_export(AxleHolderBody).stl, BackWheelAxle_export(BackWheelAxle).stl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]
2024-10-19 TODO: Make Lidar lower
    [BackWheelConnector_2_Export.stl, BackWheelConnector_M_Export.stl, BackWheelStopper_2_Export.stl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]
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2024-11-07 Make sure that pwn is off before on to prevent short circuit
    [pwm_utils.cpp]
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2024-11-18 Make the backwheel centered
    [BackWheelConnector_2_Export.stl, BackWheelStopper_2_Export.stl, CE3V3KE_BackWheelAxle.3mf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]
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2024-11-18 Fix Raspi Pico not running
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2024-11-19 Fix context in i2c_slave_utils
    [i2c_slave_utils.cpp, main.cpp]
2024-11-19 Fix i2c_master
2024-11-19 Fix log printing
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2024-11-20 Fix combine align line
    [main_lidar_testv1.cpp]
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2024-11-22 Fix camera angle TODO: Fix detectPillar when there're two frontWall
    [main_lidar_testv1.cpp]
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2024-11-24 Fix lidarDataProcessor
2024-11-24 Fix gyro drift
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2024-11-25 Add trafficLight avoidance system
    [obstacleChallenge.cpp]
2024-11-25 Fix MotorGear
    [TopTBoneLinkageBodyBody_Export.stl, TopWheelLinkageBody_M_Export.stl, WheelAxleBody_M_Export.stl]
2024-11-26 Save TrafficLight before move to prevent misinterpretation
    [obstacleChallenge.cpp]
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
